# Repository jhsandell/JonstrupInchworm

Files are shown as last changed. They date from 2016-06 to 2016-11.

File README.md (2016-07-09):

# Jonstrup Inchworm 3D Printer

## This is the source repository for building a Jonstrup Inchworm 3d printer.
Here you will find all CAD and STL files, as well as description of the kinematics and illustrations.

Read about [the INCHWORM machine](/themachine.md).
You can also browse [the STL-files](/stl) or read about [printing the parts](/docs/printing.md)

The machine is basically a 2D delta printer for the XY plane, and the rails (*) "go in the wrong direction".
The z-axis is a regular cartesian rail. 

(*) There is only one rail.

## The Name
The effector, arms and sliders may look like a Geometridae larvae moving along the x-axis. 
Compare it to the [Geometridae larvae locomotion](https://www.youtube.com/watch?v=ncx4o-W9R2c). 
And to keep up with inventive printer names, I decided to name my variant of the INCHWORM machine 
_Jonstrup_; a local town, which is pronounceable in English.



## Development Only

__This design is still a development project.__
CAD files are subject to change without notice, as features and tweaks are implemented.

The firmware is in the [Marlin_Inchworm repository](https://github.com/jhsandell/MarlinDev_Inchworm)

## Contact
<tbd>

## Credits
<Jens Henrik Sandell>

## License
Copyright 2016 Jens Henrik Sandell, all rights reserved for the Jonstrup Inchworm hardware design.

Marlin Firmware License is governed by [the projects license statement](https://github.com/MarlinFirmware/Marlin/blob/RC/README.md#license). 
All additions or modifications made to the firmware under the _Inchworm Fork of MarlinDev_, is 
subject to the Marlin Firmware License 
Statement.

> I intend to release the Jonstrup Inchworm hardware design as open source.
> Give me some time to read up on the GNU GPL...

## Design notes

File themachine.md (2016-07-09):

# Jonstrup Inchworm 3D Printer

## The Machine
This page explains the motivation for building a novel 3D printer with a unique kinematics. Design choices 
will be described in no particular order.

## Background
I discovered the 3D printing and associated Maker hype around 2010. For more than a year I just sat in front of 
my computer, and gobbled up loads of youtube videos, and trawled endless seas of webpages. In 2012 I finally 
found the funds (outside the household budget) for procuring a 3D printer: a RepRapPro Mendel (mono / legacy).
At the same time I started flying RC model aircraft. And the primary purpose for buying a printer was
to print spare parts for the model aircraft when they _eventually_ crashed.

Later, I had the wish to print larger volumes, like aircraft wings, but the machines on the market did not scale
properly with costs, and to make matters worse, all seemed to take up way to much tabletop real estate. I simply
could not fit those into my cramped cave.

> have you noticed how most designs scale almost equally on all three axis' ?

So I wanted to build a machine that could print a long and narrow object. Build platform should have some ridiculous
dimension on at least one axis: 2000mm (... and counting). (*)

(*) Well, being limited by the length of my desk, the x axis is almost 1800mm. But during development the 
the right-hand endstop is placed at 600mm.

## Primary design points
- When build volume increases, you want the build platform to be static. Accellerating a huge platform back 
and forth is neither good for the object you are printing nor the machine itself. Oscillations will occur and
shake the machine apart.
- A static build platform could also be the base for the machine. A disused kitchen tabletop would fit the
purpose; its structurally strong, its heat resistant, and to some point isolating.
- It has to sit on my desk, which I use for other things, so it cannot be supported on the front 
side, or be enclosed like a Makerbot, a Ultimaker or a CNC machine.
- With increasing dimensions, the down-bending of the structural parts has to be considered. So first option 
was to use a hollow 2020 aluminium tube. A square tube is more stiff than a cylidrical of same cross section, 
and a hollow tube weighs less than a V-slot beam.
- All structural parts should be source-able from the local home depot. I bought tubing, and M5 leadscrews from 
Bauhaus.dk and Silvan.dk. I sourced M3 screws/washers/nuts, and electronics from various webshops.
- Controller, stepper motors and hotend from various 3D printer webshops. 

## Secondary design points
Taking inspiration from the [locomotion of a Geometer Inchworm (Youtube)](https://www.youtube.com/watch?v=ncx4o-W9R2c) 
and the Kossel Delta printer I developed some novel solutions. Basically, the machine is a hybrid 
of __2D delta (x- and y-axis) and 1D cartesian (z-axis)__.
And almost at the same time I discovered [Paulo Gonçalves Tuga (OpenBuilds)](http://www.openbuilds.com/builds/reprap-tuga.390/).
- Instead of a Scott-Russel linkage i decided to implement a parallelogram. Any fans sitting at the effector 
hotend would induce some gyro torque when the head rotates. It might not be much, but I intuitively liked this better. 
- Two carriages share one rail. The stepper motors and drive belts fit easily side-by-side on the same rail. It just a 
design challenge to make unique parts all over the place. The carriages fit the square tube tightly and slides without 
any bushings, and without lubrication.
- The Z-axis is a regular cartesian rail with stepper motors and a M5 leadscrew. I printed the bushing in 
nylon and tapped it manually, hoping that it would be a low friction solution. Later I might change this to 
a TR8x2 trapez leadscrew. I just have to by a TR8x2 TAP from Ebay.
  - by the way: the Z-axis might be _any height_. Just buy two longer leadscrews and 2020 aluminium tubes.
- The parallellogram construction might also be a problem: the effector and hotend assembly induces torque on 
the X-rail. So the z-position might vary depending on Y-position. 
- The max print speed is as usual determined by the heaters ability to melt the plastic, as well as the 
steps-per-second rate of the controller . And print quality is determined by the vibrations
dependent on the accelleration and stiffness of the machine.
- The cooling fan (in the E3D hotend) should blow the heat away from all plastic parts. At the same time it 
can also function as a structural part, holding the hotend to the effector arm. 

# Proof of Concept
The idea just popped into my mind... And it might be a heritage of having played a lot with LEGO Technic as a kid.
So I sat down and printed a POC, using some smooth rods from an scrapped inkjet printer.
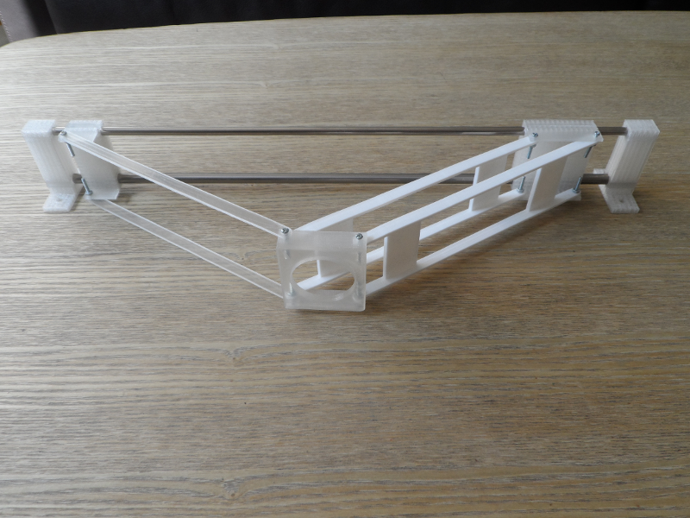
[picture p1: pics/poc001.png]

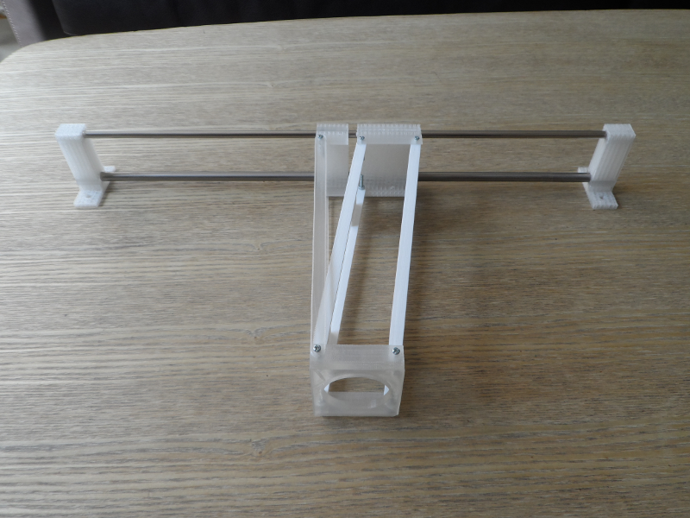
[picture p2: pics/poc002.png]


Please observe: The effector plate (with the large hole) was printed lying down, while the two sliders were standing up (on its right side end) to allow printing the holes for the rails. The XY plane and the Z-axis on my printer has bad calibration, so the holes of the effector and the sliders are not equally spaced. The effector rotates a bit, which can be seen in the first picture, compared to the second. (it may also be due to the hot plastic _sagging during printing_, when it is not completely solidified). 

The conclusion is: print all effector parts in the same orientation, and preferably in one pass, if your printer can have all three parts on the build plate simultaneously. 

## Bending
The effector arms should be stiff and not bend. The hotend will have some weight and gravity will do its job on the machine. 
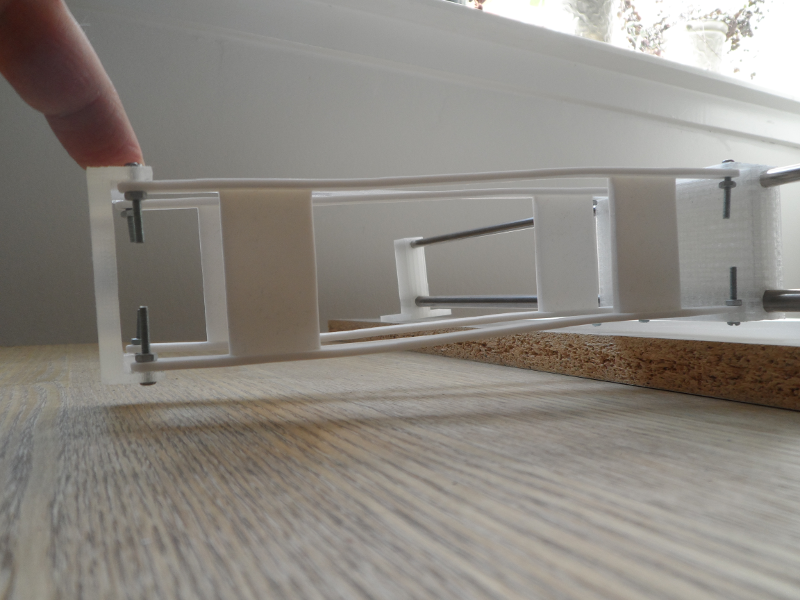
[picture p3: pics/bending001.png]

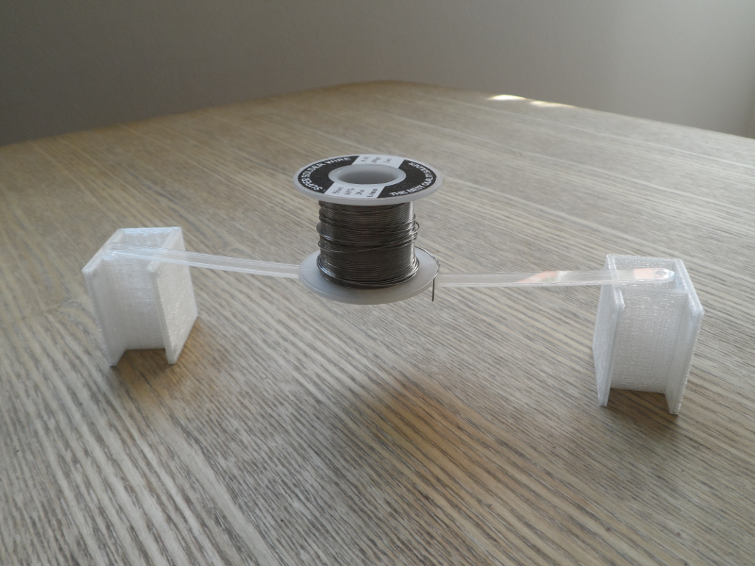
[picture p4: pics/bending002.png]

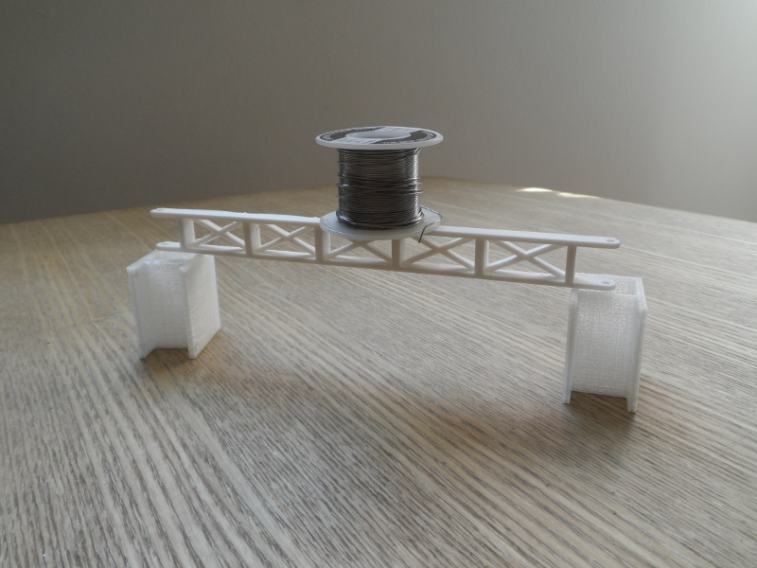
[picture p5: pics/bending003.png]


## Iterations
The design evolved over time... A lot of PLA was spent on prototypes.
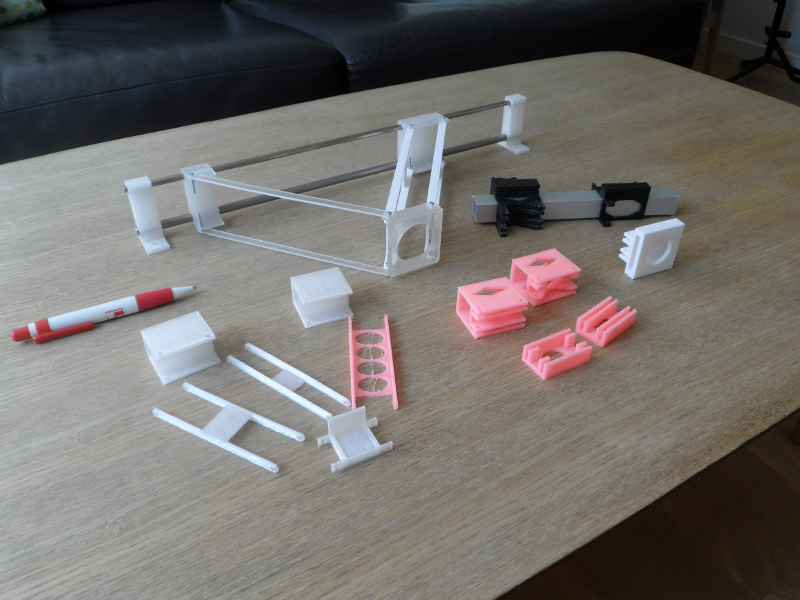
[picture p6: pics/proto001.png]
proto001


This is an early assembly picture. The x-axis is scalable: buy a longer 2020 alu tube and longer GT2 belts. Same goes for the z-axis and the leadscrews. The effector arms implies a 2*L cost on the x-axis. I intend to explain this later... 
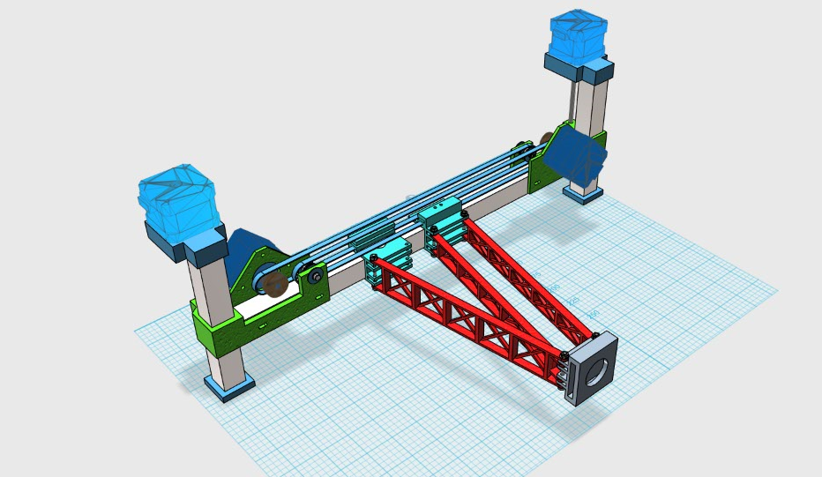
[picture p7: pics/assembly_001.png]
Assembly001


## Kinematics 
> describe the Inchworm kinematics

> insert a picture

> describe the motion of the sliders.

> describe the motion of the effector.

> describe the different arm lengths and the trade-offs

> describe the inverse kinematics math.

> describe the forward kinematics math. (used for homing?)

## Firmware development
The kinematics calls for a open source firmware, where the math can easily be put in, without having to write
all from scratch. I tried to work with Repetier and Marlin. The firmwares have pros and cons, but in the end I 
settled on Marlin.  I have tried to make the changes as readable as possible. A fairly skilled programmer will
be able to port the code.
Either way ... my limited hobby-time presents a challenge in keeping up the primary Marlin Firmware development.
I have restarted my efforts twice to introduce the INCHWORM functions without breaking compatibility with the DEV branch.

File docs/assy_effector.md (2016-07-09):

todo: Write about the effector assembly.
And add some pictures.

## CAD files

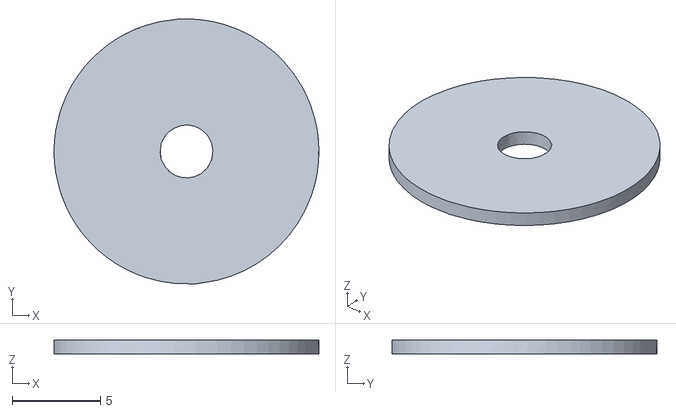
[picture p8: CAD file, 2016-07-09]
stl/beltshim001.stl
15.0 x 15.0 x 0.8

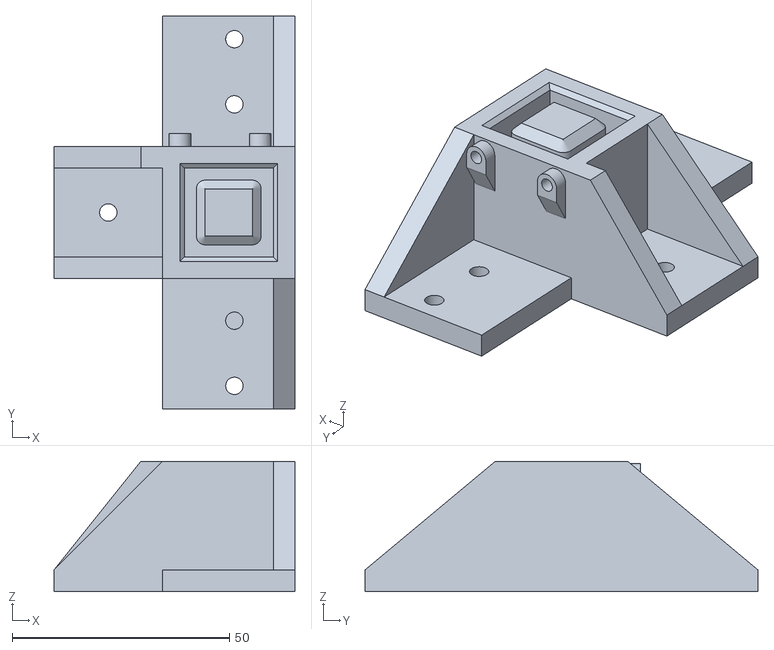
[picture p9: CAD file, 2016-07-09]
stl/foot001.stl
55.5 x 90.5 x 30.0

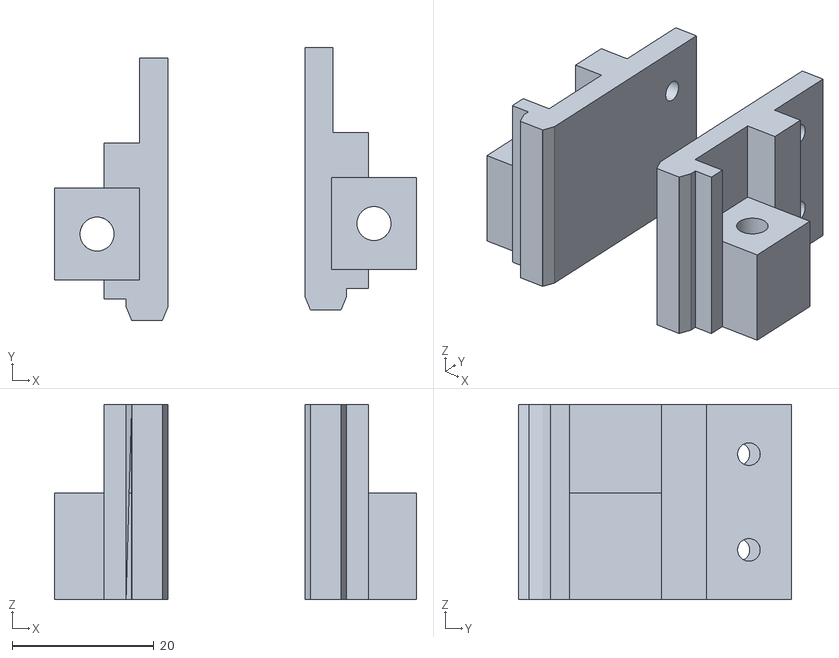
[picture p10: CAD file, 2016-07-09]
stl/zbushings001.stl
51.0 x 38.5 x 27.5

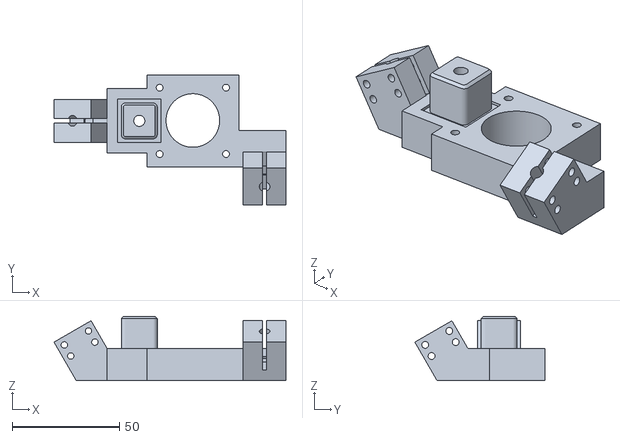
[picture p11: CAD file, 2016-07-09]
stl/foot004.stl
108.3 x 60.9 x 30.0

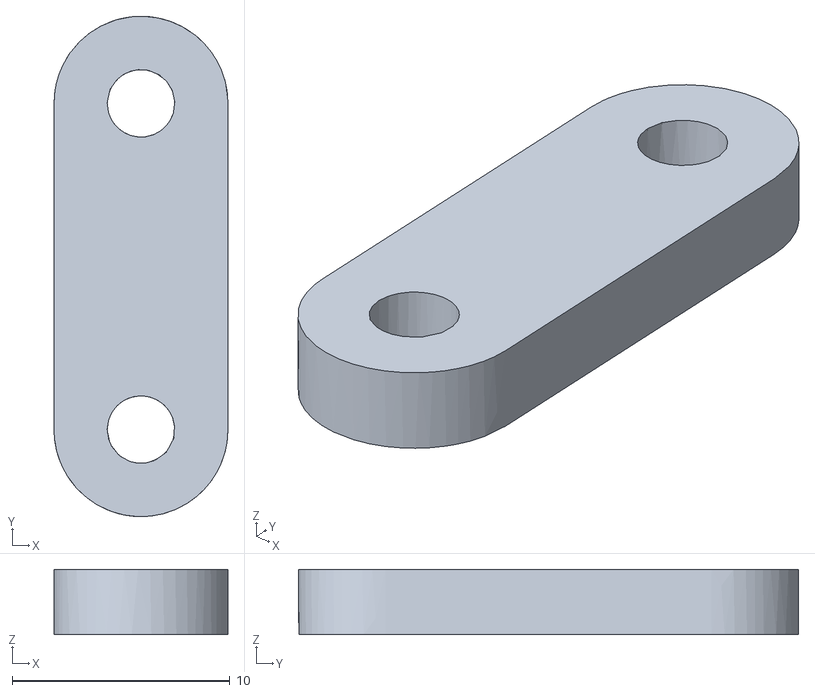
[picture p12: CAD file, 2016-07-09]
stl/clamp001.stl
8.00 x 23.0 x 3.00

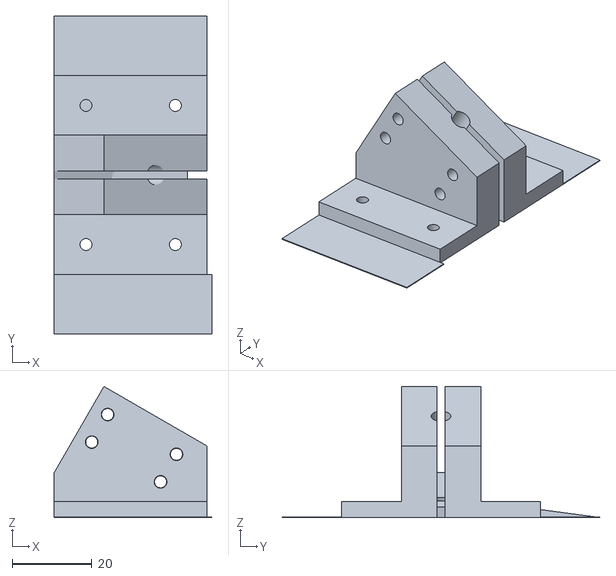
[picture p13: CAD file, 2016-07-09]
stl/foot002.stl
39.7 x 80.0 x 33.0

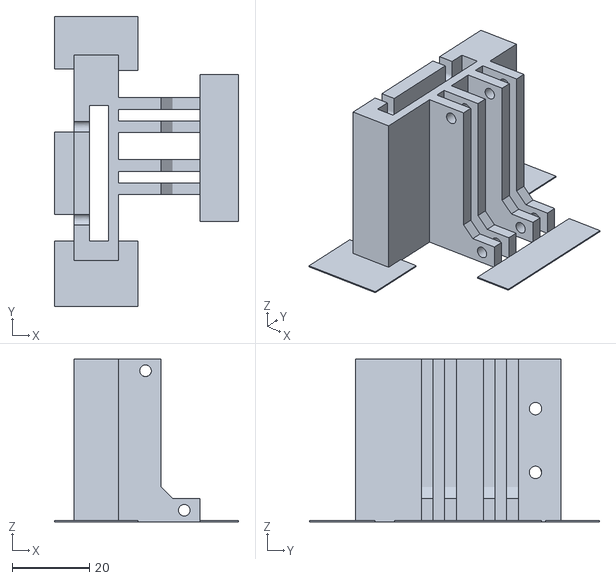
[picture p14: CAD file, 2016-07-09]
stl/eff001.stl
47.5 x 74.9 x 42.0

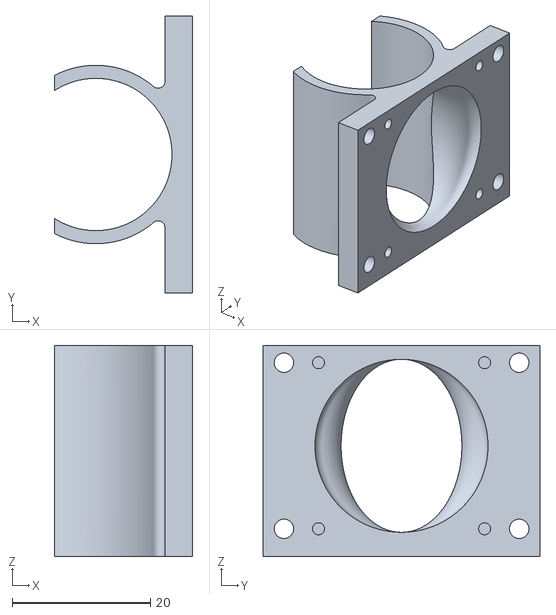
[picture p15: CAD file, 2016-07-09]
stl/eff006.stl
20.0 x 40.0 x 30.5

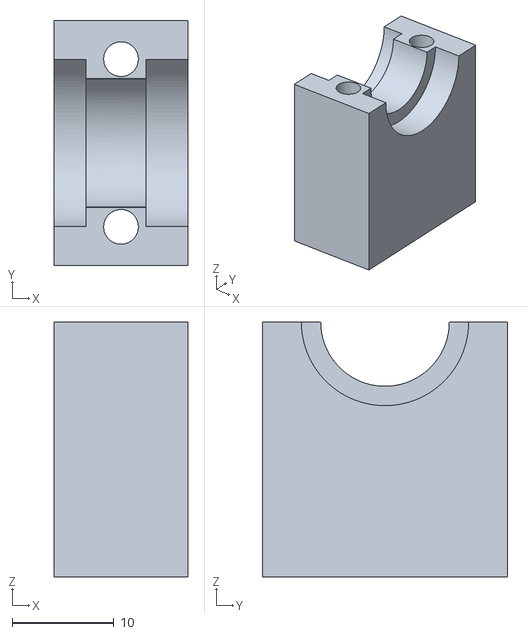
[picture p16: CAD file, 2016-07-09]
stl/eff004.stl
13.1 x 24.0 x 25.0

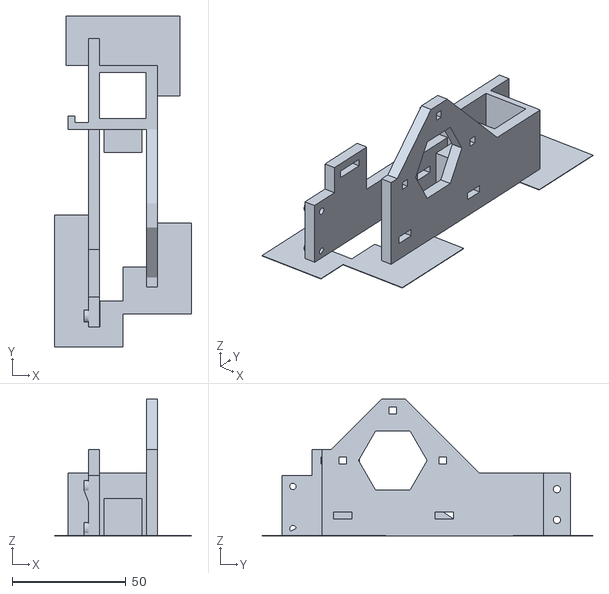
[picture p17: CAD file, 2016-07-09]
stl/xmount001.stl
60.1 x 145.0 x 60.0

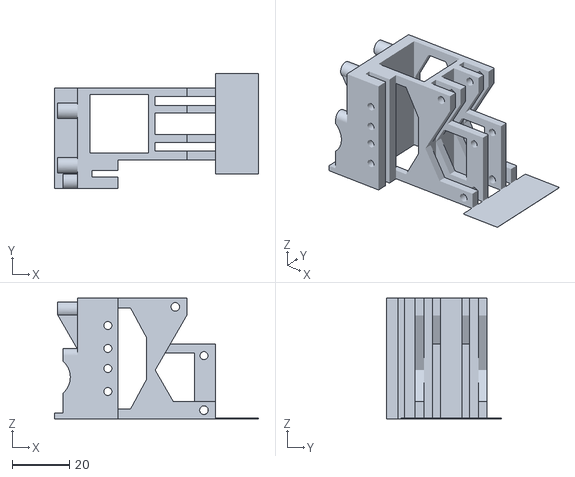
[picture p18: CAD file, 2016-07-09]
stl/eff003.stl
71.1 x 40.1 x 42.0

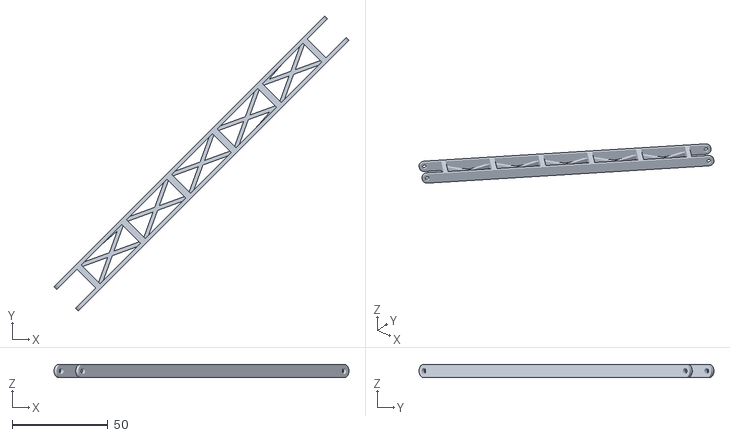
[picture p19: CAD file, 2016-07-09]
stl/eff008.stl
154.1 x 154.1 x 7.00

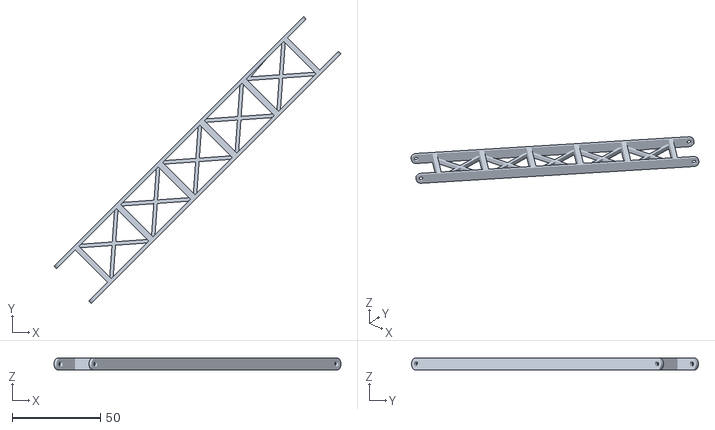
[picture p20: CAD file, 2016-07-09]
stl/eff007.stl
162.6 x 162.7 x 7.00

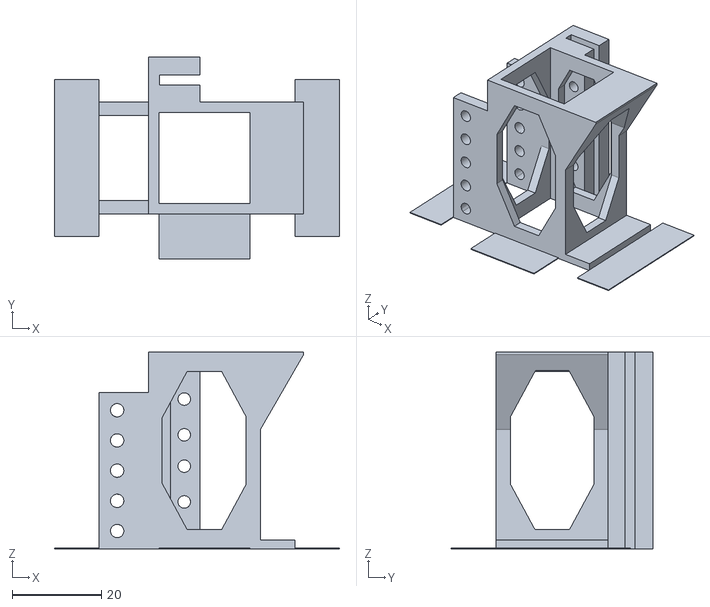
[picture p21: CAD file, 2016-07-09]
stl/eff002.stl
63.7 x 45.1 x 44.0

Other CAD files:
stl/foot003.stl
stl/xmount002.stl
stl/eff005.stl

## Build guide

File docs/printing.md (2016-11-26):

# Printing
This document describes various aspects of printing all the parts for the Jonstrup Inchworm. Look in the tables how 
many copies you need to print.

## PLA and NYLON
Most parts are printed in PLA. Three parts are printed in Taulman 618 nylon. Nylon is chosen either 
as a _lubricant-free_ bushing on the z-axis, or as the _heat tolerant_ fan shroud on the E3D hotend. 

## Alignment and Brims and No Support 
The STL's shall be printed in the alignment shown in the pictures. This assures that _critical dimensions_ 
are controlled by the same axis on all parts. In other words: do not rotate objects if holes or dimensions 
are supposed to be identical. _It will affect the INCHWORM's final precision_. 

Several large objects have _manual brims_. The brims counters warping and assures adhesion to the 
buildplate, without having to put an automatic brim all the way around the objects edges. A few large 
objects shall be printed with automatic brim.

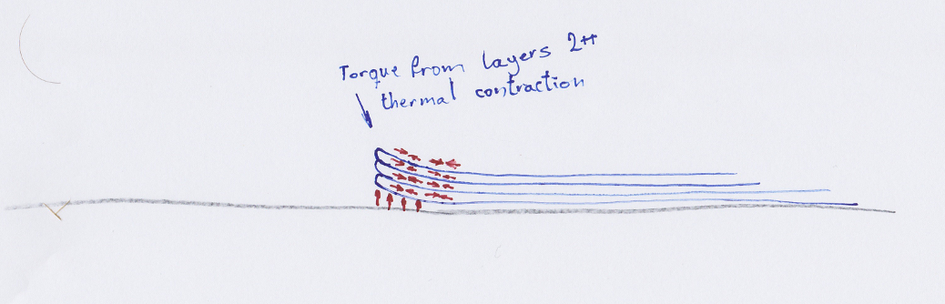
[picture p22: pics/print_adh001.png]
without a brim
 

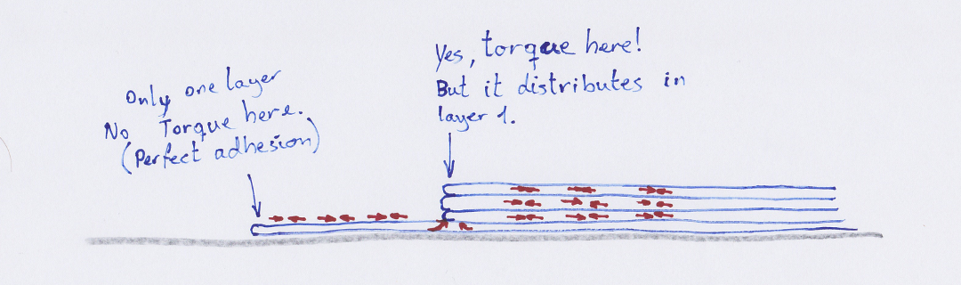
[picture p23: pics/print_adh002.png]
with a 1-layer brim - manual or automatic


Example of a brim that counters warping.
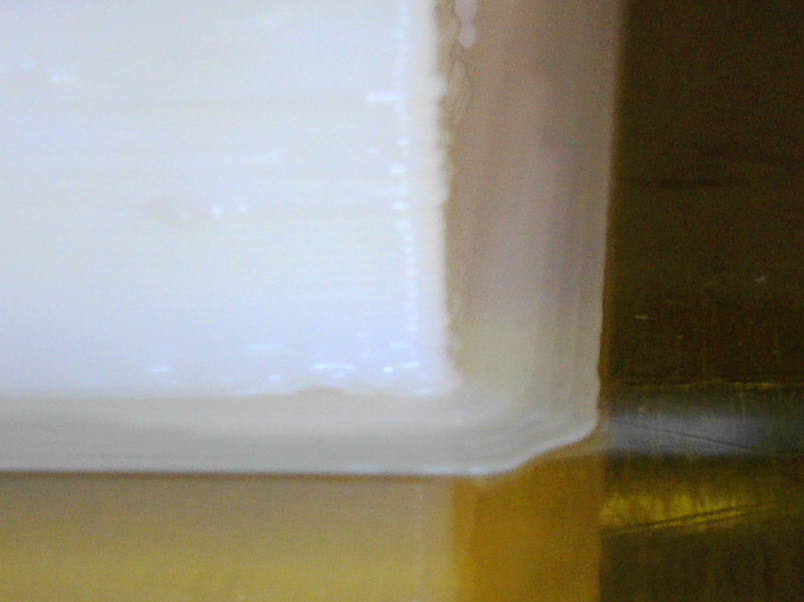
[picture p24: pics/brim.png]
brim


The objects can be printed without support material. Angles of overhangs are only 30 degrees of vertical. Most
holes require _bridges_ in one way or another. Please have a look at the picture of the two x-axis motor mounts. You can also see how screw holes are built with manual support.

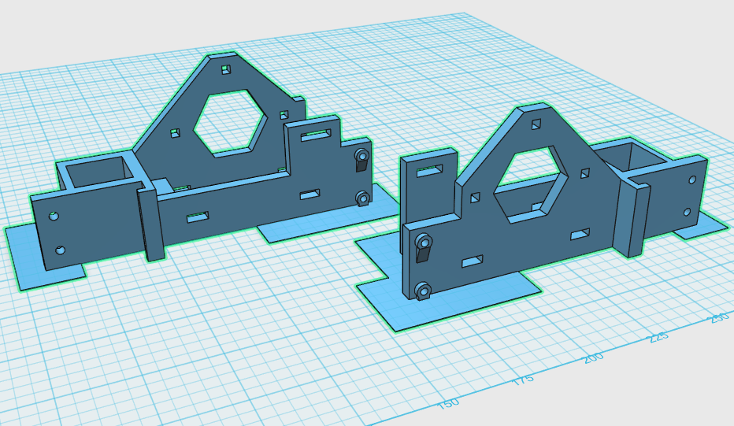
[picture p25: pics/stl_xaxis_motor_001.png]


## STL parts list

The STL files have been reduced with in Meshlab with "Quadric Edge Collapse Decimation". Please let me know, if there are any faults in the files.

<table>
  <tr>
    <th>Name</th>
    <th>File</th>
    <th>Copies</th>
    <th>Pics</th>
  </tr>
  <tr>
    <td>Effector</td>
    <td><a href="/stl/eff001.stl">eff001.stl</a></td>
    <td>1</td>
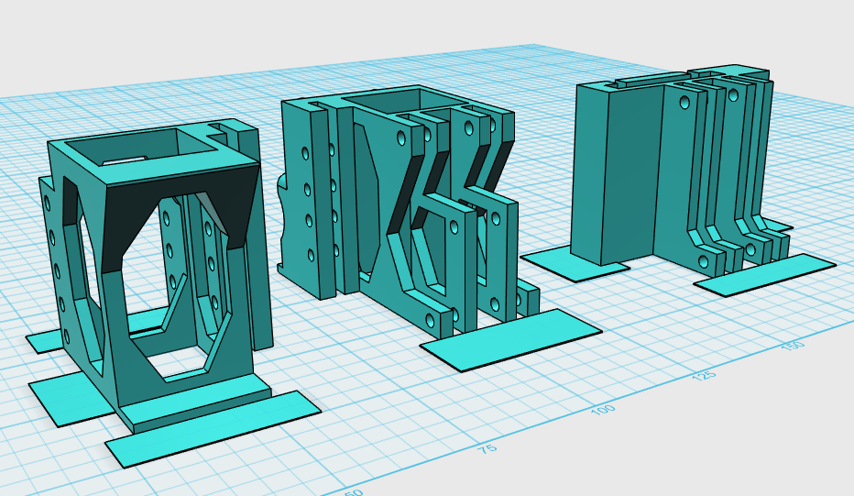
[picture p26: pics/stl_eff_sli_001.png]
    <td rowspan="3"></td>
  </tr>
  <tr>
    <td>Slider Left</td>
    <td><a href="/stl/eff002.stl">eff002.stl</a></td>
    <td>1</td>
  </tr>
  <tr>
    <td>Slider Right</td>
    <td><a href="/stl/eff003.stl">eff003.stl</a></td>
    <td>1</td>
  </tr>
  <tr>
    <td>Groove mount block</td>
    <td><a href="/stl/eff004.stl">eff004.stl</a></td>
    <td>1</td>
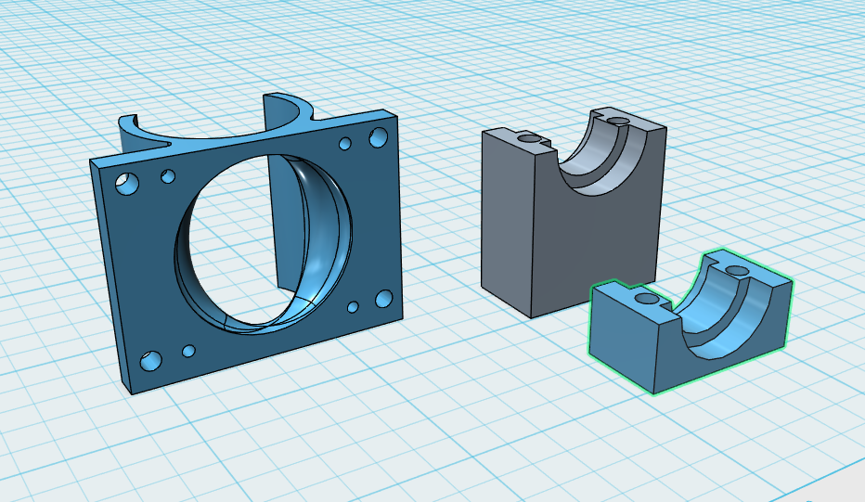
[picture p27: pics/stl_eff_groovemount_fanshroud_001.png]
    <td rowspan="3"></td>
  </tr>
  <tr>
    <td>Groove mount clamp</td>
    <td><a href="/stl/eff005.stl">eff005.stl</a></td>
    <td>1</td>
  </tr>
  <tr>
    <td><B>NYLON</B> Fan shroud (for E3Dv6 hotend)</td>
    <td><a href="/stl/eff006.stl">eff006.stl</a></td>
    <td>1</td>
  </tr>
  <tr>
    <td>Effector wide arm</td>
    <td><a href="/stl/eff007.stl">eff007.stl</a></td>
    <td>2</td>
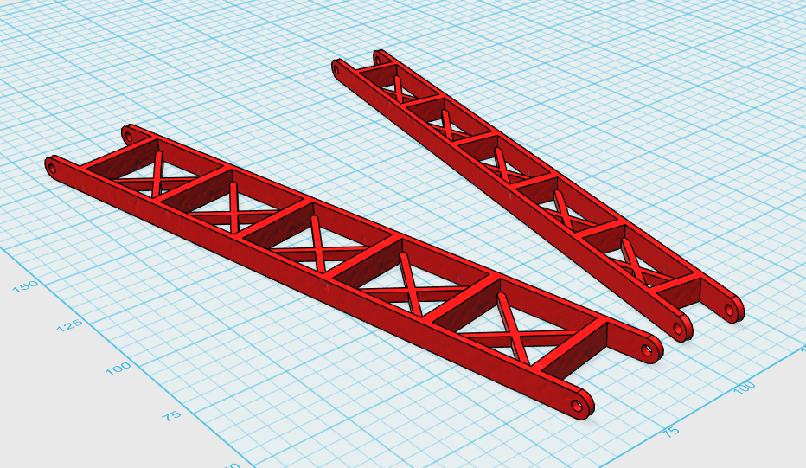
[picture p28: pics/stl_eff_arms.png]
    <td rowspan="2"></td>
  </tr>
  <tr>
    <td>Effector narrow arm</td>
    <td><a href="/stl/eff008.stl">eff008.stl</a></td>
    <td>1</td>
  </tr>
  <tr>
    <td>Left X-axis motor mount</td>
    <td><a href="/stl/xmount001.stl">xmount001.stl</a></td>
    <td>1</td>
    <td rowspan="2"></td>
  </tr>
  <tr>
    <td>Right X-axis motor mount</td>
    <td><a href="/stl/xmount002.stl">xmount002.stl</a></td>
    <td>1</td>
  </tr>
  <tr>
    <td>Belt shim</td>
    <td><a href="/stl/beltshim001.stl">beltshim001.stl</a></td>
    <td>4</td>
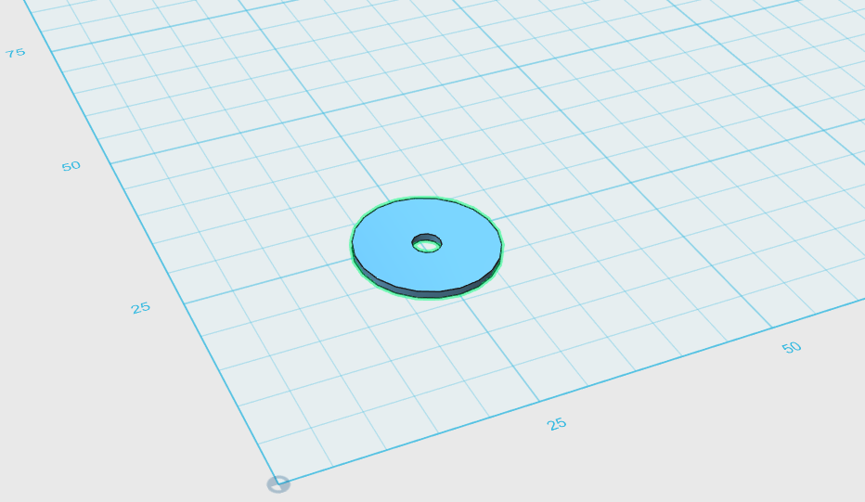
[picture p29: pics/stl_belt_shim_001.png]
    <td></td>
  </tr>
  <tr>
    <td>Cable clamp</td>
    <td><a href="/stl/clamp001.stl">clamp001.stl</a></td>
    <td>4</td>
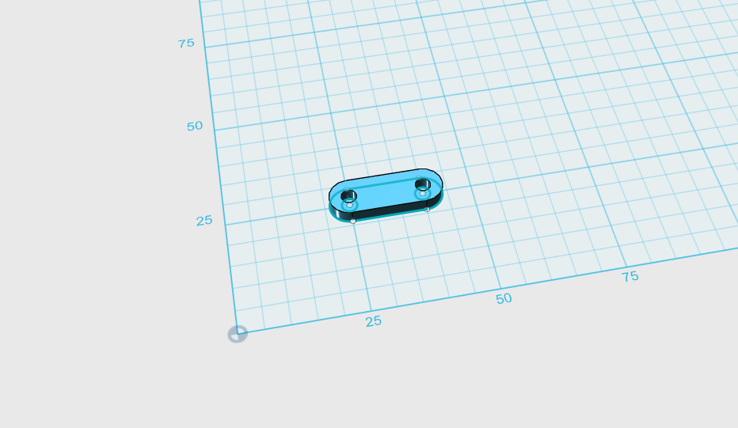
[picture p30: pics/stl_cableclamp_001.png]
    <td></td>
  </tr>
  <tr>
    <td><B>NYLON</B> z-axis bushings</td>
    <td><a href="/stl/zbushings001.stl">zbushings001.stl</a></td>
    <td>1 set</td>
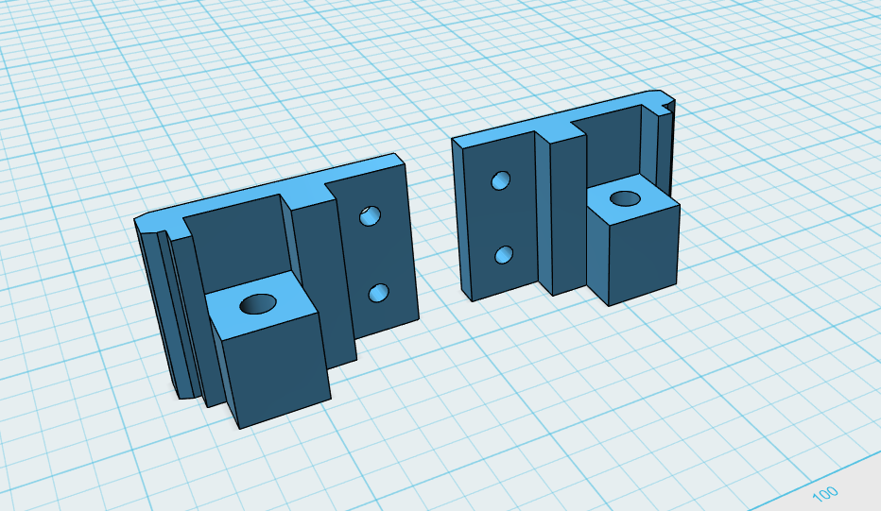
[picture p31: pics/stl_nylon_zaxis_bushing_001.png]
    <td></td>
  </tr>
  <tr>
    <td>Z-axis 2020 foot</td>
    <td><a href="/stl/foot001.stl">foot001.stl</a></td>
    <td>2</td>f
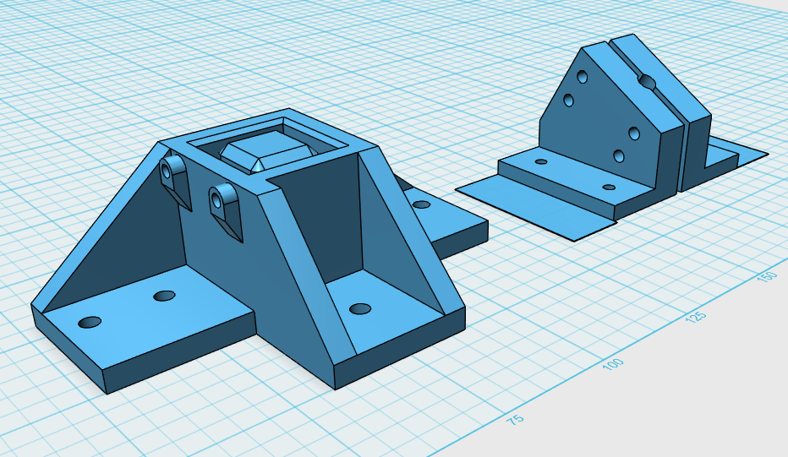
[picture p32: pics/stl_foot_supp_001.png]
    <td rowspan="2"></td>
  </tr>
  <tr>
    <td>Z-axis support foot</td>
    <td><a href="/stl/foot002.stl">foot002.stl</a></td>
    <td>4</td>
  </tr>
  <tr>
    <td>Z-axis left motor mount</td>
    <td><a href="/stl/foot003.stl">foot003.stl</a></td>
    <td>1</td>
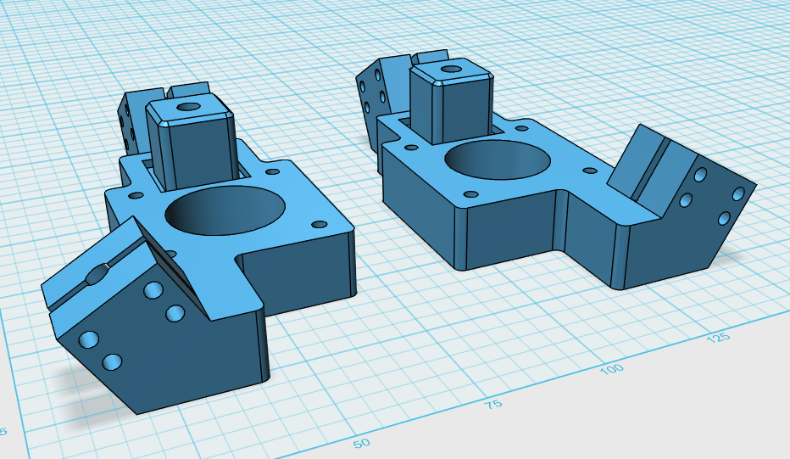
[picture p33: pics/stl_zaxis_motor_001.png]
    <td rowspan="2"></td>
  </tr>
  <tr>
    <td>Z-axis right motor mount</td>
    <td><a href="/stl/foot004.stl">foot004.stl</a></td>
    <td>1</td>
  </tr>
</table>

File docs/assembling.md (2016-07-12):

# todo: Write the _primary_ text on assembling the machine.

## Printing
Reference the [file about printing](/docs/printing.md) 

## Everybody needs vitamins
And for the Jonstrup Inchworm, you will need the following parts. 

**Please note: There are no exact amounts on how many screws, washers and nuts you need. Buy a bag of 100 pieces for each type.**

- NEMA17 stepper motors, 5x
- RAMPS compatible electronics, 1x
- E3D v6 hotend
- 12V power supply
- CAT6 ethernet cable. (its shielded. its cut into several lengths. motors and endstops are _NOT_ carried in the same cable.)
- crimp plugs, assorted no. of poles
- endstops, 5x
- M5 leadscrew, 1m, 2x (cut into several lengths. also used for supports.)
- flexible couplers (btw. stepper and leadscrew.)
- GT2 pulleys, 2x
- GT2 belt, 10m
- 623zz ball bearing, 2x
- 2020 square aluminium tube, 20mm x 20mm x 3000mm (cut to lengths 2000,300,300) 
- M3 hex cap-head screws, assorted lengths
- M3 washers, standard
- M3 washers, wide
- M3 nuts
- M3 nylock nuts
- M3 leadscrew, 20cm, 1x (cut into several lengths. used for the groovemount blocks on the effector.)
- M5 nuts, (for adjusting the supports)

Reference the subchapters:
- assy_leftz.md
- assy_rightz.md
- assy_xrail.md
- assy_effector.md

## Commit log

2016-06-25 more text first license statement
    I cannot say it enough times: the Marlin Firmware is governed by its License Statement. All my contributions to the firmware is subject to the Marlin Firmware License Statement.
2016-07-09 stl files...
2016-07-09 assembly text - started
